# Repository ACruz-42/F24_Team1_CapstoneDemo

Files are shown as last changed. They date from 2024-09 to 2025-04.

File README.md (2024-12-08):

# SECON 2025 Hardware Competition Robot - TNTech Team

## Summary of Requirements

This repo provides the documents and reports written to produce the TNTech autonomous robot for the SECON 2025 Hardware Competition.
The following link goes to a video that shows a general overview of the requirements.

https://attend.ieee.org/southeastcon2025/wp-content/uploads/sites/642/IEEE-SoutheastCon-Hardware-Competition-Game-Mining-Mayhem.mp4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

The robot needs to autonomously navigate the field, collect materials, sort materials, deposit materials, and deposit containers.

## Capabilities

As a high level overview, the robot will need to navigate to materials outside the cave and collect them.
They will be sorted and deposited into their designated containers, which will be held by the robot.
After collecting all materials outside the cave, the robot will enter the cave.
It will then navigate to and collect materials inside the cave.
These will also be sorted and deposited into their designated containers.
After collecting all materials inside the cave, the robot will exit the cave and move to the designated zone to deposit the containers.
Finally, the robot will place a team beacon into the beacon mast.

## Salient Outcomes

Robot hasn't been constructed yet.

## Project Demonstration & Images

Picture pending of 3d model.

Give a link to a video of the project being demonstrated. The video should be hosted on the capstone youtube.

Below the video link show some well-taken, appropriately sized images of the project.

## About Us

### Team

Give a brief bio for each team member and their broad contribution to the project (no need to be terribly specifc).

Sean Borchers
Alexander Cruz
Samuel Hunter
Alejandro Moore
Dakota Moye

### Faculty Supervisor

Syed Ali Asad Rizvi

### Stakeholders

This project is important to TNTech as a whole and specifically to the ECE Department.

### Recognitions

Some portions of this robot were based off of the modular robot made Spring 2024.

Link to repo: https://github.com/lchapman42/Control-Sensing-Wireless-Charging-Robot

## Repo Organization

Give the layout of the repo and what can be found where. Make it easy on those who are interested by making the headings of the various things in this section clickable links to the relevant folder or file in the repo.

### Reports

[Link to Reports folder](https://github.com/ACruz-42/F24_Team1_CapstoneDemo/tree/a463979d4f1928be542ba7baea590573b307fce3/Reports)

This folder includes the Project Proposal, Conceptual Design, and Detail Design.

Project Proposal discusses the high-level problem, high-level solution, specifcations, constraints, and measurements of success.

Conceptual Design discusses the solution for each subsystem with each subsystem split appropriately.
It lists the team members who work on each subsystem.
There is a block diagram to show how the subsystems connect.
There is an operation flowchart to show how the robot should be interacted with by users.
There is a high level operation flowchart that shows the general actions for the robot.

Detail Design is split into a separate document for each subsystem.
Each Detail Design discusses how each subsystem will be constructed and implemented.

### Documentation

Documentation folder has only been used for electrical schematics and 3d models so far.

In the documentaion section information regarding the documentation that is required and how it should be organized is given.

### Software

No software has been written yet.

In the software directory of the repo information regarding how each team is expected to document software can be found.

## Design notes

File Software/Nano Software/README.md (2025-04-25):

## Overview

This folder contains the final Jetson Nano code presented at the SECON 2025 Hardware Competition. The Jetson Nano code was redesigned to work as a leader or controller to the Arduino follower or responder code. The Jetson Nano had all of the control and autonomous software. The Arduino had low level interface with motors for PWM signals and for reading in most sensor data.

This folder also contains one other program that was used to test the OTOS. qwiic_otos_ex1_basic_readings.py is a copy of the example provided by Sparkfun for testing the OTOS with a python controller, such as the Jetson Nano. It has been slightly modified to only record the last data point after a set timer ends. It is not used for running the robot.

The following link goes to the Arduino Follower Software readme. This provides information on how the data is sent back and forth and how the arduino controls the lower level logic: https://github.com/ACruz-42/F24_Team1_CapstoneDemo/blob/c923fd8bf496c972fe1331faf40be674d2dc7530/Software/Arduino_Follower_Software/README.md

## Dependencies

smbus2, other otos, camera, python3.11.smth

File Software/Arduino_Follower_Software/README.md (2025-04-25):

## Overview

This folder contains the final Arduino code presented at the SECON 2025 Hardware Competition. The Arduino code was redesigned to work as a follower or responder to the Jetson Nano leader or controller code. The Jetson Nano had all of the control and autonomous software. The Arduino had low level interface with motors for PWM signals and for reading in most sensor data.

## Dependencies
1. TimerOne by Stoyko Dimitrov, Jesse Tane, Jérôme Despatis, Michael Polli, Dan Clemens, Paul Stoffregen
2. ezButton by ArduinoGetStarted.com
3. Servo by Michael Margolis, Arduino

Dependencies 1 and 2 have to be installed. Dependency 3 came preinstalled in the Arduino IDE. The first two were installed through the Arduino IDE library search function.

## Use
### Input
The Arduino Follower Software takes in a set of inputs. These are supposed to come from the Jetson Nano code, but it can be manually input. The format is a packet or string of 10 ints in format "int,int,int,int,int,int,int,int,int,int" without the quotation marks. The first two need 201 options for data type. The rest need 3 options, which means 2 bits would work. In the center column of the following table is the allowed inputs. 

One example is "50,-20,1,1,0,0,1,-1,0,1". This sets left wheel speed to forward 50%, right wheel speed backward 20%, auger forward, sweeper forward, does nothing to beacon arm, does nothing to beacon gripper, opens GSC gripper, closes NSC gripper, does nothing for GSC leaner, and moves NSC leaner to pickup angle. If one of the components is already in a specific state, it will stay in that state until sent a different one. This means everything will keep moving until told to stop. For the servo control, they will keep their angle until told to change, and then will keep that angle. The table below lists the inputs in order of placement along the packet. The table shows input to be controlled, range of input control, and what happens for that range.

In the final edition of the code, the GSC arm was not used and is manually set to be 0 in the code.

|input type|input available|input action|
|:-|:-|:-|
|left wheel speed|-100 to 100|0 to 100% speed. Negative is backwards and positive is forwards.|
|right wheel speed|-100 to 100|0 to 100% speed. Negative is backwards and positive is forwards.|
|auger forward, backward, or off|1, 0, -1|1 is forward, or desired direction. 0 is stop. -1 is backward, or undesired direction.|
|sweeper direction and on or off|1, 0, -1|1 is forward, or desired direction. 0 is stop. -1 is backward, or undesired direction.|
|beacon arm preset location|1, 0, -1|1 moves beacon arm to holding angle and is initial angle, 0 is nothing, -1 moves beacon arm to placement angle|
|beacon gripper open or closed|1, 0, -1|1 closes beacon gripper and is initial state, 0 is nothing, -1 opens beacon gripper|
|Geodinum Shipping Container (GSC) Gripper open, close, or stop|1, 0, -1|1 opens GSC gripper, 0 stops, -1 closes GSC gripper|
|Nebulite Shipping Container (NSC) Gripper open, close, or stop|1, 0, -1|1 opens NSC gripper, 0 stops, -1 closes NSC gripper|
|GSC Leaner preset location|1, 0, -1|1 is pickup angle, 0 is nothing, -1 is storing angle|
|NSC Leaner preset location|1, 0, -1|1 is pickup angle, 0 is nothing, -1 is storing angle|

### Output
The Arduino Follower Software outputs a set data when it receives a command. These are supposed to be sent to the Jetson Nano, but it can print to any serial. The format is a packet or string of 7 variables in format "bit,bit,int,int,bit,bit,bit" without the quotation marks. In the center column of the following table is the available outputs.

In the final edition of the code, the current sensors were not used and are manually set to 0 in the code.

|output type|output available|output action|
|:-|:-|:-|
|current sensor for sweeper|1, 0|1 means the sweeper has stalled, 0 means it has not|
|current sensor for auger|1, 0|1 means the auger has stalled, 0 means it has not|
|GSC pressure sensor|0, 100|0 to 100% pressure. 100% pressure is max pressure sensor can handle.|
|NSC pressure sensor|0, 100|0 to 100% pressure. 100% pressure is max pressure sensor can handle.|
|GSC limit switch|1, 0|1 means limit switch, or button, is pressed, 0 means it is not pressed|
|NSC limit switch|1, 0|1 means limit switch, or button, is pressed, 0 means it is not pressed|
|light sensor|1, 0|1 means the start LED sensor sees more light than the ambient light sensor, 0 means the opposite|

## Hall Effects
In the last edition of the code, a sorter was made to process the hall effects and object sensor. The goal was to flip the servo for the sorter flap back and forth according to the hall effects and object sensor. This ended up not working due to the hall effects having some issues discussed in the Experimental Analysis. While still in the code, sorter.cpp and sorter.h currently does nothing important.

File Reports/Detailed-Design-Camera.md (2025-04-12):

# Detailed Design for Object and Line Detetion
## Function of Subsystem
The function of this subsystem is to provide the location of the astral materials, lines, and walls on the game field, as well as read the april tags and then provide this information to Master Control, so that Master Control can plot an effecient path to pick up all astral material, as well as sort the shipping containers at the end of the match, while unsuring the robot does not collide with anything from the front.

## Specifications and Constraints 
### Specifications
1. The robot shall act autonomously [S1].
2. The camera shall detect the Nebulite [S2-vii].
3. The camera shall detect the Geodinium [S2-viii].
4. The robot shall be able to detect the walls of the arena, walls of the cave, and cave entrance. Rule S03 states that if the robot causes field damage, the team will be penalized. Detecting walls stops the robot from causing damage by moving into it. The camera will be the only sensor on the front and will need to do the listed objectives [S4].
5. The camera shall read April Tags to help with Specifications 1, 2-v, 2-vii, 2-viii, and 2-ix [C1].

These Specifications stem from the the game rules and are intended to set into strict goals the methods by which the robot will score points and therefore do well in the competition. 

### Constraints
1. The camera will be able to work in both light and dark conditions
2. In order to keep costs down the robot will only have 1 RGBD camera
3. The robot will be able detect the white lines on the game field

Constraint 1 stems from the fact that the game field will have a dark cave, which will contain astral material, and as such the robot will need to enter the cave and search for astral material.
Constraint 2 stems from socio-economic concerns, the camera will comprise roughly 15% of the robots total budget, and as such it will be advantageous if only one is used to keep costs down and allow more room in the budget for other sybsystems. 
Constraint 3 stems from the robots need to use the white lines to navigate the game field as well as score points by sorting the filled shipping containers.

## Proposed Solution
In order to meet the specifications and constraints the robot will need an RGBD camera, this camera will be able to pick out the RGB values of the astral matrials and lines on the game field against the dark background of the game field, this will help meet Specifications 2 and 3 and contraint 3.
The camera will also be able to pick out the depth, or distance from the camera, of the astral material, the shipping containers, and the walls of the game field, this will help meet Specifications 1, 2, and 3.
The information from the camera and the other sensors as on the robot will be used by an object detection algorithm to the robot where the objects are on the game field, mainly the astral material, walls, and shipping containers, this will help meet Specifications 1, 2, 3, and 4.
The image data from the camera will also be used by a line detection algorithm to find the white lines on the game field to assist in navigation and sorting of the shipping containers, this will help meet constraint 3.
Finally the image data will undergo an image processing algorithm which will allow it to read the april tags, much in the same way a phone can read a qr code from a picture or screenshot, this will help meet specification 5.

## Interface with Other Systems
The camera will connect to the Jetson nano using a USB-C 3.1 Gen 1, this connection will transfer the image data, which includes including RGB values and depth values, the camera will also be powered through this connection and will take a 5V supply[2]. 
The primary responisibility of the camera will be to find the astral material on the game field and then send its location to Navigation and Master Control for the purpose of finding an effecient path to pick up all astral material.
The next responsibility of the camera will be to find the white lines on the game field and then send their locations to Navigation and Master Control for the purposes of navigation and sorting the shipping containers. 
The camera will also be responsible for reading the april tags and sending their values to Master Control for the purpose of sorting the shipping containers into the correct telemetry zones. 
The camera will also aid in locating the walls of the game field, and will be responsible for making sure that the robot does not crash into anything from the front.
Since both Navigation and Master Control and the detection and image processing algorithms will all be housed on the Jetson Nano so all communication betweeen these algorithms will be done internally.

## Buildable Schematic
Buildable schematic

## FlowChart
A quick note for the flowchart, the robot will start and then it will go about the tasks shown in the flow chart, these tasks will continue until some kind of interrupt occurs, either all astral material will be collected, or the robot will run out of time and will need to sort the shipping containers without collecting all astral material.
Operational Flowchart

## Analysis
### The Camera
The camera will be an Intel Realsense D435 RGBD camera, this camera was chosen for its wide FOV of 87° × 58°, as well as its depth range of .3 m to 3 m. Also this camera uses stereoscopic depth technology which is needed as infrared projection technology cannot be used in conjuction with the infrared camera that is part of the game field in the cave. The camera will take a 5V voltage supply that will be transfered through a USB-C 3.1 Gen 1 connection which will also be used to transfer the image data to the Jetson Nano. This connection has a maximum information transfer rate of 5 GB per second. The cameras depth values will be greater than 98% accurate at 2 meters. The camera will send both the RGB values of the picture as well as the depth values of the picture to the Jetson Nano where these values will be used by various algorithms as described below[2].

### Object Detection Algorithm
The object detection algorithm will work similarly to many generic object detection algorithms, in that it will take an image and will scan through the pixels to find specific patterns and differences is RGB values, however it will be much simpler than most object detection values as we will be mainly trying to detect one type of object with a known size and more importantly a known RGB value and a known shape, which will be against a dark background.
This will make it easy to pick out the astral material as all the algorithm will have to do is search for that specific RGB value and the seperate each little "ball" of that color, then the algorithm will go to the depth data of the image and look at the place where it found the propor color and find the depth of that area.
Since the camera will be at a fixed place on the robot we will be able define a constant axis at the front of the robot, then using the values of RGB and depth we will be able find the angle of the astral material compared to the axis at the front of the robot and then use the depth to find the distance from the axis which will give each astral material a polar coordinate value. 
This polar coordinate value can then be transformed into cartesian coordinates on the robots internal grid system.[3]
One valuable tool that will help with this process is openCV, which is a large open source computer vision and machine learning software library[5]. Using libraries from openCV will simplify the above process greatly as there are already useful libraries written that can search for specific monochromatic colors like the ones we will need for the astral material[6].

### Line Detection Algorithm 
The line detection algorithm will work much the same to the object detection algorithm in that it will take an image as input and will use a simplified version of a generic line detection algorithm to pick out the white lines against the dark background of the game field.
Since the lines on the game field are in fixed positions the robot can use the shape and composition of these lines to determine where they belong on the game field and therefore where it is in comparison to them.
Since the lines on the game field are in fixed positions the robot can use the surrounding context such as walls to determine how far away the lines are, or in other words, the depth of the lines. Similar to with object detection we can make use of openCV where preexisting libraries exist using methods such as the hough transform to find all the lines in an image[1]. 

### Image Processing for April Tags
The image processing algorithm for the april tags will activate once Master Control sends a signal that the robot is in position, it will then scan the image much in the same way the the detection algorithms did, except it will be looking for the april tags, which should be easy to locate as it will be a box of white and black.
Once the april tag has been located it will look at the specific pixels and decode them into a number, much like a QR code scanner.
it will then send the value to Master Control along with the locations of the lines from the line detection algorithm to tell the master control which telemetry zone to put the shipping containers in[4]. As april tags are becoming more commonly used in robotics there are also preexisting libraries that can aid in reading them, that will yet again come from openCV[7]. 

### Image Processing for the Walls
The image processing for the walls is a simple algorithm that will measure the distance between the robot and the walls and will alert the robot if it gets too close to a wall. Due to the way the collection system for the astral material is being designed the camera will be the only forward facing sensor and as such will be responsible for making sure the robot does not collide with anything from the front.

## Ethics 
The camera will come as a fully built and developed device and as such full credit for camera design will be given to those responsible, the camera will also have an infrared projector which will aid in depth sensing capabilities, this infrared projector is safe for use in close proximities to humans. 
The detection and image processing algorithms will also be simplified versions of generic algorithms and as such proper credit will be given for any code or methods that are taken from other sources.
Finally the subsystem will have user manual explaining the subsystems function and operation in a way that others can clearly understand the operation of the subsystem.

## BOM
| Manufacturer | Part Number | Distributor | Part Number | Quantity | URL  |Price |
|---|---|---|---|---|---|-|
| Intel| 82635AWGDVKPMP| Intel| 82635AWGDVKPMP| 1|[Intel Realsense D435](https://store.intelrealsense.com/buy-intel-realsense-depth-camera-d435.html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)|314.00 USD|

## Refrences 
[1]“OpenCV: Hough Line Transform,” docs.opencv.org. https://docs.opencv.org/3.4/d9/db0/tutorial_hough_lines.html  

[2]“Intel ® RealSense TM Product Family D400 Series Datasheet Intel ® RealSenseTM Vision Processor D4, Intel ® RealSenseTM,” 2024. Available: https://www.intelrealsense.com/wp-content/uploads/2024/10/Intel-RealSense-D400-Series-Datasheet-October-2024.pdf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  

[3]“What is Object Detection in Computer Vision?,” GeeksforGeeks, May 10, 2024. https://www.geeksforgeeks.org/what-is-object-detection-in-computer-vision/  
‌  
[4]X. Ling, “How to Optimize QR Recognition Performance by Image Preprocessing and Parameter Tuning,” DEV Community, Sep. 13, 2021. https://dev.to/yushulx/how-to-optimize-qr-recognition-performance-by-image-preprocessing-and-parameter-tuning-24p8 (accessed Nov. 28, 2024).

[5]OpenCV, “About OpenCV,” OpenCV, 2018. https://opencv.org/about/

[6]“Real time object color detection using OpenCV,” GeeksforGeeks, Oct. 14, 2021. https://www.geeksforgeeks.org/real-time-object-color-detection-using-opencv/

[7]A. Rosebrock, “AprilTag with Python,” PyImageSearch, Nov. 02, 2020. https://pyimagesearch.com/2020/11/02/apriltag-with-python/
‌
‌
‌
‌
‌
‌

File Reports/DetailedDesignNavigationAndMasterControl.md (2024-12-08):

# Detailed Design
## Function of the Subsystem

The navigation and master control subsystem utilizes a Jetson Nano as the core of the robot's systems. The master control portion of this subsystem interfaces with the various sensors, such as the LiDAR and OTOS (Optical Tracking Odometry Sensor) sensors, and motor control. The navigation portion of this subsystem is based on an internal 2-dimensional grid. Based on the positional feedback from the sensors and event completion feedback from the Arduino microcontroller parsed by the master control subsystem, the navigation subsystem outputs a desired rotation and distance that the master control subsystem sends to the motor control Arduino in the form of high-level serial commands over a USB connection. Additionally, with the assistance of the Sensors and Object Detection subsystems, respectively, this subsystem will handle localization of the robot (i.e. its position on an internal map of the game board) and the placement of the astral material on the robot's internal map. It will manage all of this using a state machine that transitions its states based on the time remaining and positional feedback from the various sensors and event completion feedback from the  motor control Arduino.

## Specifications and Constraints

### Specifications:
1.  The Robot shall act autonomously (Specification 1 [1]). This is necessary for compliance with Game Manual 1
2.  The Robot shall be able to navigate to and position itself for the following tasks (Specification 2 [1]). This is necessary to maximize potential points.
	i. Navigate out of Landing Pad (i)
	ii.  Navigate within 3 seconds of Start LED (ii)
	iii.  Navigating into the cave (iii)
	iv.  Navigate to correct shipping pad (v)
	v.  Navigate to and allow for placement of team beacon (ix)
3.  The Robot shall account for background interference (Specification 11 [1]). This is to help reduce potential failure points.
### Constraints:
1.  The Robot shall stay on the game field (Specification 5 [1]). This is necessary for the safety of the team and all IEEE SECON staff members.
2.  The Robot shall cease all operation after 3 minute timer is done (Specification 10 [1]). This is necessary for the safety of the team and all IEEE SECON staff members.
3. The Robot shall immediately cease operations upon the usage of the emergency stop button (Specification 7 [1]). This is necessary for the safety of the team and all IEEE SECON staff members.

## Overview of Proposed Solution

The proposed solution centers around a hybrid navigation system combining preprogrammed paths with dynamic pathfinding for specific tasks. The system relies on a state machine and an event queue to generate and coordinate high-level navigation commands with the microcontroller associated with the motor subsystem. Sensor feedback from LiDAR and odometry ensures real-time localization and adaptive positioning.

### **Core Components and Operation**

1.  **State Machine**  
    The majority of the robot's navigation tasks, such as moving between predefined locations like the landing pad, cave, and shipping pad, are handled via preprogrammed paths defined in a state machine. A state machine is a way of organizing potential states that, in this case, the robot can be in, and the transitions between these states. The routes these states mean algorithmic pathfinding can be avoided, reducing the need for heavy computation during a match.
    
   2.  **Event Queue**  
The event queue serves as a decoupling mechanism, separating the state machine and high-level logic from time-sensitive tasks [2]. Once a desired position or action is determined by the state machine, it is added to the event queue. The queue then processes these events sequentially, sending high-level commands—such as the required rotation and distance—to the microcontroller, which handles motor control. After the Arduino sends a command saying it's processed the current event or a period of time without movement, the next event is sent. This design allows the Jetson Nano to continue processing other high-level tasks, such as processing sensor data or computing navigation algorithms. 

2.  **A-Star Pathfinding**  
    The A-Star algorithm is employed for states that involve picking up astral material. The way that A-Star works is as a form of Dijkstra's algorithm (an algorithm that explores each node in order of its distance from the starting node) [3]. In essence, A-Star is used as a way to balance finding the shortest path along with a given heuristic (in this case, proximity of the path to the nearest material) [4].  The state machine chooses the furthest astral material. A-Star plots a path to this material. The heuristic function in the A-Star algorithm heavily prioritizes paths  with astral material. If any astral material remain after reaching the destination, this process is repeated until either all astral materials are gathered or the time allotted runs out. This approach balances optimal pathfinding with the competition's time constraints, allowing the robot to maximize points.

4. **Sensor-Driven Feedback Loop**  
    Positional data from LiDAR and odometry sensors provide continuous updates on the robot's location. This feedback ensures that the robot can accurately determine its current position and orientation, enabling adjustments when moving toward desired positions.

### **Specification Compliance**

1.  **Autonomous Operation (Specification 1)**  
    The competition forms the basis for various setpoints (static positions of the shipping containers, entering the cave, or the dynamic positions of the astral materials) . Based on these internal setpoints and feedback from the sensor subsystem and motor control subsystem, the robot utilizes a state machine to generate setpoints for the motor control subsystem. The event queue decouples the generation of these setpoints from time, and instead couples the generation with the completion of prior setpoints. The integration of the state machine, event queue, and sensor feedback ensures that the robot operates autonomously, meeting the competition’s requirements for compliance with Game Manual 1.
    
2.  **Navigation (Specification 2)**
    - Preprogrammed paths handle transitions between key locations (e.g., specifications i, ii, iii, v). The state machine holds desired positions, which the event queue determines the necessary distance from the actual position of the robot, and necessary rotation to get to that position.
    - The A-Star algorithm dynamically optimizes the collection of astral materials by balancing path length and material prioritization (e.g. specification iv, and for the collection of astral material). A heuristic that balances path proximity to astral material versus the cost of the path will be determined experimentally to find the lowest time. This can and will be done both with the physical robot, and via the Godot simulation.

3.  **Background Interference Tolerance (Specification 11)**  
    The feedback loop continuously corrects the robot's position using real-time sensor data from multiple sensors and an event completion signal from the motor control Arduino, mitigating the effects of environmental interference such as noise.

### **Constraints Compliance**    

4.  **Staying on the Game Field (Constraint 1)**  
    Predefined paths plot a course that should keep the robot within the boundaries. Real-time sensor data from the LiDAR ensures the robot stays within boundaries as a stop command will be issued to the Arduino within a certain distance, maintaining safety for participants and compliance with rules. 
    
5.  **Ceasing Operation (Constraint 2)**  
    The state machine halts all operations when the timer reaches the three-minute limit. This is currently enforced programmatically as a high-level if statement inside of the main loop of the program.
    
6.  **Emergency Stop (Constraint 3)**  
    The emergency stop button overrides all active processes, immediately issuing a stop-motors command to the Arduino, ensuring compliance with safety requirements.
## Interface with Other Subsystems

#### Inputs:
-   **LiDAR Data**: Provides distance measurements to surrounding objects for real-time localization and obstacle detection.
    -   _Input Type_: Distance
    -   _Method_: I2C

-   **Odometry (OTOS) Data**: Applies Kalman filter to IMU, and optical sensor, and outputs the result.
    -   _Input Type_: Positional
    -   _Method_: I2C
   - **Arduino Data**: Provides signal that a given event has completed, or stopped prematurely.
       -   _Input Type_: Signal
	    -   _Method_: USB
   - **Camera Data**: Uses color to determine where astral materials are on screen, then uses depth to output position of astral material. 
       -   _Input Type_: Positional
	    -   _Method_: USB
  #### Outputs:
  
 -  **Rotational Setpoints**: Tells Arduino how far to rotate robot.
	 - _Output Device_: Motor Control Arduino
	 - _Output Type_: High-Level Commands
	 -  _Method_: Serial
-  **Positional Setpoints**: Tells Arduino the distance of translation for robot.
	 - _Output Device_: Motor Control Arduino
	 - _Output Type_: High-Level Commands
	 -  _Method_: Serial
- **Stop Command**: Tells Arduino to stop immediately, in case of collision or match end.
	 - _Output Device_: Motor Control Arduino
	 - _Output Type_: High-Level Command
	 -  _Method_: Serial
## Godot Simulation
As a proof of concept for the overarching software architecture, a simulation in Godot was created. Godot was chosen for two main reasons: ease of prototyping, and the similarity of GDScript (Godot engine's inbuilt programming language) to Python. Additionally, closure (the ability for a function to retain memory outside of its enclosing scope [5]) makes the connection between state machine and event queue easier. At time of writing, this simulation is not fully operable but development is ongoing and the most up to date version (and source code) can be found at the following link. Note that support for operating systems other than Windows is not supported at this moment.

https://github.com/ACruz-42/F24-Team1-Capstone-Simulation

The state machine is only about half-way complete, but the relationship between main loop, state machine, and event queue are functional and proofs of the effectiveness of the design. That is to say, the state machine correctly outputs desired positions and rotations, but does not currently contain all states as described in the operational flow chart below. Additionally, the A-Star algorithm works but is not interconnected with the other subsystems at this moment. 
## Buildable Schematic

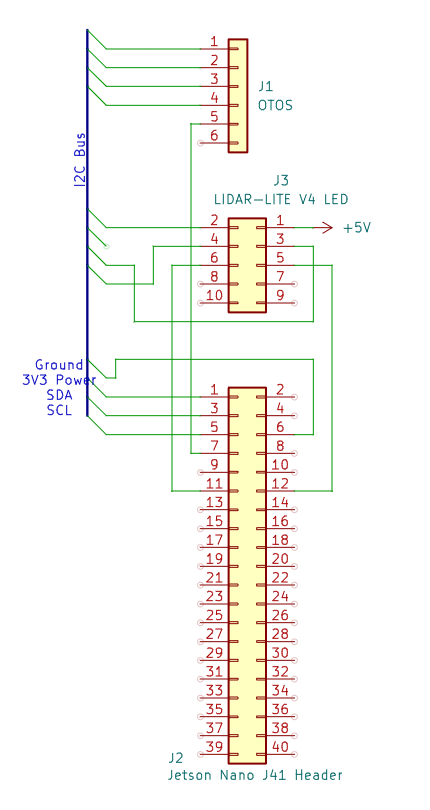
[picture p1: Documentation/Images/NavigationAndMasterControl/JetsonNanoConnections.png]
GPIO Pinout for Jetson Nano

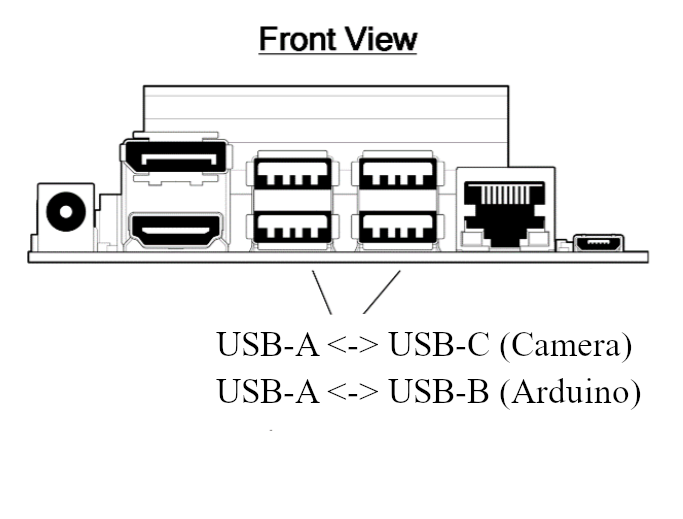
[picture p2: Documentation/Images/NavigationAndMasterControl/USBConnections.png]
Jetson Nano USB Connections

## Operational Flowchart

Operational Flow

## Hierarchy

### Highest
- **State Machine**: This provides the setpoints for the rest of the system.
	- **Event Queue**: This parses the sensor and camera subsystems, interprets the state machine's setpoints with respect to the current state, then sends commands (target location setpoints) to the Arduino.
		- **Sensor Subsystem**: This provides positional feedback to event queue.
		- **Camera Subsystem**: This provides positional feedback to event queue (with respect to astral material).
			- **Arduino**: This receives setpoints, initiates a PID control loop with the motors, then provides feedback to the state machine that the motors have finished.
				- **Motors**: The motors deliver rotational energy to the wheels, which move the robot. The related encoders provide velocity feedback to the Arduino.
### Lowest

## BOM

|Item|Manufacturer|Part Number| Distributor|Distributor Part Number|Quantity|Price
| :- | :- | :- | :- | :- | :- | :- |
|Jetson Nano|Nvidia|#945-13450-0000-100|Amazon|B0B8DMPWJL|1|$215
|Total||||||$215|

Jetson Nano purchasing link: https://www.amazon.com/onboard-Robotics-Machine-Learning-Version/dp/B0B8DMPWJL

## Analysis

-   **Program Structure: State Machine, Event Queue, and Main Loop**  
    The decision to structure the software into a state machine, event queue, and main loop provides several advantages in maintainability and efficiency.
    
    -   The  state machine dictates the robot's high-level behavior, handling navigation between predefined locations and managing of transitions predictably and reliably. Additionally, clear delineations between states allow for easy debugging and experimentation
    -   The event queue serves as a time-independent intermediary, decoupling the state machine from real-time motor control. By abstracting motor commands to the Arduino, the event queue allows the Jetson Nano to continue executing high-level tasks without being constrained by execution delays.
    -   The main loop integrates the state machine and event queue together, ensuring continuous processing of sensor data and high-level commands. This structure ensures the robot can react dynamically to new information without compromising ongoing tasks, such as the operation of the emergency off-button or the detection of astral material. This design has already shown promise in the Godot simulation, where the interdependencies between these components have been successfully implemented, even if partially.
-   **Choice of Godot for Simulation**  
    Godot was selected as the simulation platform for its ease of prototyping and its GDScript language, which closely resembles Python—the programming language used on the Jetson Nano. This similarity allows for a smoother transition from simulated logic to real-world implementation.
    
    -   **Prototyping**: Godot’s user-friendly interface and node-based structure made it possible to iterate on designs quickly, enabling fast debugging and validation of core concepts such as the interaction between the state machine and event queue.
    -   **Code Translation**: GDScript’s support for closure simplifies the connection between the state machine and event queue. Python is similar in both its indent-based code, and programming with support for closure. This structural alignment ensures the simulation’s code can be easily transferred to the actual robot.
    -   **Progress**: While the simulation is not fully operational, its current development demonstrates the effectiveness of the chosen structure. The integration of A-Star for astral material collection and the foundational elements of the state machine are already functional, further validating this choice.
    
    The simulation also provides a controlled environment to test edge cases and refine the robot’s behavior before physical implementation, significantly reducing development risks.
    
-   **Jetson Nano Over Raspberry Pi 5**  
    The Jetson Nano was selected over the Raspberry Pi 5 due to its superior compatibility with AI and machine vision tasks and its lower power consumption.
    
    -   **Processing Capabilities**: The Jetson Nano’s GPU is optimized for deep learning and computer vision tasks, enabling efficient real-time processing of sensor data (particularly the camera) and the A-Star algorithm. This capability directly supports the subsystem’s need for parallel computational power, particularly for tasks like localization and navigation.
   
    -   **Power Efficiency**: Operating between 10-20W, the Jetson Nano consumes significantly less power than the Raspberry Pi 5’s 25W, aligning with the project’s constraints on battery life. This efficiency ensures the robot can operate effectively within the competition’s time limit without exhausting power resources.

## Execution Plan

The current execution plans revolves around finishing the Godot simulation. The navigation portion of the navigation and master control subsystem should be trivial with the ability to use the GDScript code as a reference. Once all the ordered parts arrive, more importance will be placed on integrating the Jetson Nano with the various sensors and connection to the Arduino. By swiftly implementing the master control subsystem, development on the other subsystems can take place faster.

The simulation should, assuming current development pace, be finished before next semester.

The parts necessary for the other subsystems should arrive by the next semester.

Although the competition takes place in March, the plan is to finish by February and test during its duration. This leaves January and February to implement the navigation and master control systems. As the navigation subsystem should be easily transferrable, and the master control subsystem will be implemented with the assistance of the other subsystems, completing the robot should be a viable task.
## References

[1] “Game Manual 2 V1.1.3,” IEEE, 2019. Accessed Nov. 26th, 2024. [Available Online] https://docs.google.com/document/d/1fN7bsJFpCJur66JkueRHXtlybt0m7QSY4Nn62lHAnrc/edit?tab=t.0
‌[2]R. Nystrom, “Game Programming Patterns”. United States. Genever Benning, 2014.
[3] GeeksforGeeks, “Dijsktra’s algorithm,” GeeksforGeeks, Nov. 19, 2018. Accessed Nov. 26th, 2024.  [Available Online] https://www.geeksforgeeks.org/dijkstras-shortest-path-algorithm-greedy-algo-7/
[4] “A* Search Algorithm in Python,” GeeksforGeeks, Apr. 17, 2024.  Accessed Nov. 26th, 2024.  [Available Online] https://www.geeksforgeeks.org/a-search-algorithm-in-python/
‌[5]Rahul K, “An Introduction To Closures and Decorators in Python,” Earthly Blog, Jul. 18, 2023. Accessed Nov. 26, 2024. [Available Online]https://earthly.dev/blog/python-closures-decorators/

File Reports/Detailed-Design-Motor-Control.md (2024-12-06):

# Detailed Design
## Function of the Subsystem 
The motor control subsystem is meant to carry out the functions of the robot based on sensory input and the needs of the given situation during the competition as driven by the Master Control. The drivetrain motors will actuate the translation of the robot and will change the speed based on factors such as weight, obstacles, time remaining, among other crucial considerations for obtaining the maximum amount of points. Additional mechanisms on the robot will be used to collect, sort, and distribute astral material in their appropriate containers. These mechanisms will also require motor control, and they will use various types and configurations of motors. 

The drivetrain motor system functions as the feedback-based reaction center for the robot’s processes. It uses the input taken in from sensory data, such as object and line detection or map navigation, and follows the commands given to it from a microcontroller to perform the physical responses of the robot. Motor control can include the following components: a microcontroller (MC), motor, motor driver, encoder, power supply, and specific components for noise reduction and circuit protection [1]. The motor microcontroller carries the digital signal commands for the designated motor to operate as required. However, the power that the MC needs to function is not enough in comparison to what the motor needs. Therefore, it is essential to have a component that can step up the power for the motor while still using the MC for commands. This is the purpose of the motor driver. The motor microcontroller sends a digital signal to the driver using PWM to set the desired motor speed. Encoders that detect the motor shaft speed/position to provide the actual speed of the motors are useful for completing a closed loop feedback system, such as with PID control [2]. All logic control circuitry, which includes the microcontroller and encoders, will receive low voltage from the power subsystem, while the motor driver will receive high voltage in order to provide the high power needs of the motors. 

Several types of motors are utilized for the astral material collection and sorting process. Brushed DC motors are used for the mechanisms that have continuous feedback based on desired versus actual motor speed, such as with the overall robot movement and the collection of astral material. Separate motor drivers are connected to these motors and provide the appropriate power based on PWM input from the microcontroller. Linear actuators will be used for clamping onto the shipping container, and they will need drivers as well for directional control of the extension of the actuator. Servo motors will be used for the material sorting mechanism via a system of gates, lifting the shipping container, and controlling the positioning of an arm that will place the Team Beacon.  

The selection process for choosing a brushed DC motor versus a servo motor for the collection and sorting applications is based on the torque and speed requirements of each system. For the drivetrain motors, the motor control system will be constantly running and collecting feedback, going at a high speed and changing directions quickly. Therefore, a circuit that can efficiently modify the power level to the motors would be ideal, and a brushed DC motor/driver pairing using PWM control would satisfy the need for efficient speed control. However, there will be a need for motors that are not continuously running and collecting data but may instead be performing a precise sequence of movements that are based on position control and feedback. This is where a servo motor would prove to be useful, as the servo position is able to be finely controlled by applying the correct pulse length from the microcontroller [4]. Both brushed DC motors and servo motors have high torque applications, but with different usage cases. Brushed DC motors will have high torque at a low speed [12], likely due to a heavy load. Servo motors will also have high torque for heavy loads, but the context for their use will be in precise positional control over the mechanism that carries the load. Servos also have three different sizes depending on desired torque level: micro, standard, and giant [4]. Micro and standard sizes will be used for the mechanisms discussed in this report. 

## Specifications and Constraints 
#### 1) The motors shall be capable of meeting the requirements of the Game Manuals and shall be appropriate for their designated mechanisms (detailed below). 

#### 1a) The motors shall operate at a voltage of less than 30 volts [S12]. 

Rationale: This voltage limit was put in place due to the requirements placed by Game Manual 1 at Rule 16 for the purpose of safe but capable robot operation. 

#### 1b) The drivetrain motors shall be able to accelerate up to a calculated desired speed for each navigational path that can enable the robot to traverse the whole field twice in under 3 minutes using a given distance, angle of approach, and the time allotted. 

Rationale: This specification was put in place to verify the capabilities of the motors for efficient speed control and to create a plan for the Motor Control subsystem to meet the objectives set by Navigation and Master Control.  

#### 1c) The motor specs for each mechanism shall account for a proper balance of speed, torque, and inertia to implement the best-suited motors for the task. 

Rationale: This balance was considered because even though some components and methods may meet general specifications, the goal is to search for the best solution that can optimize the overall process for collecting points.  

#### 1d) The drivetrain motors shall be able to operate under a load of up to 12 kg. 

Rationale: The 12 kg threshold is the maximum allowed mass permitted for the heaviest configuration of the robot, as per Game Manual 1. 

#### 1e) The sorting and collecting motor systems for astral material shall be able to transfer and carry the load of at least one astral material at a time (3D printed icosahedrons, 48.2 g each for Geodinium). 

Rationale: In order for the sorting and collecting process to function, at least one astral material must be able to traverse the whole system from pick-up to deposit at a time, and therefore the mass of at least one astral piece will be considered for load-handing from the motors. 

#### 1f) The Cosmic Shipping Container motors shall be able to carry and support most of the load from a full container of astral material – 18 Geodinium for a total of 867.7 g. 

Rationale: A full container of material accounts for the worst-case load scenario for the motors, with Geodinium being slightly heavier than Nebulite due to the internal magnets. 

#### 2) The motor control subsystem shall be capable of an immediate termination of functions induced by an emergency stop button [S7]. 

Rationale: This command for immediate stoppage brought about by E-Stops is required by the Game Manual 1 at Rule R04 and enables increased protection for the equipment, arena, and personnel on site.  

#### 3) The motors shall be capable of speeds allowing the robot to traverse the game field at least twice (once for collecting astral material, and once for the return trip) within three minutes (the length of a match) [S2]. 

Rationale: This specification was put in place so that the robot would be equipped to at least reach any point on the map and return to deposit material for points. On this one trip, the current plan is to find the most optimal route around the field for material collection, but making it so that the robot would have the ability to quickly and efficiently traverse the entire field and back would account for any suboptimal deviations within the time limit. 

#### 4) The motors shall be capable of reversing the robot in the case that reversing the robot is the only method of not damaging the game field walls [S4]. 

Rationale: This was of consideration due to the need for the robot to be able to have escape maneuverability near field walls, with damage to the field being grounds for a penalty.  

#### 5) The motor subsystem shall be designed in such a way that accounts for background interference in the competition environment [S11]. 

Rationale: This specification was put in place due to the requirement set by Game Manual 1 at Rule R13, in which competitors should account for naturally occurring electrical noise in the competition environment that may interfere with the lower-level circuitry.  

#### 6) The motor subsystem shall have a user manual that explains functionality and design intent [C2]. 

Rationale: This specification was placed in order to follow a precedent set by prior capstone groups for creating documentation that lays out the necessary design information for any future work on a similar project or building on the same project.  

#### 7) The motor subsystem shall adhere to applicable requirements in standard IEC 60204-1 pertaining to electrical supply, electromagnetic compatibility, emergency stop, and control circuit protection [C3]. 

Rationale: This constraint was put in place for the motor subsystem to abide by established electrical codes, with this particular IEC standard laying out several different types of safety measures that would be applicable to the motor control circuitry. It aligns with the request from the Game Manuals in the mandatory inclusion of E-Stops. It also presents the necessity to include components that promote overcurrent protection and proper grounding [3]. Clear labels and documentation for the circuit components involved are also needed by this standard [3].  
 
## Overview of Proposed Solution
### Drivetrain
The solution will incorporate several layers of command for the robot movement. The first layer will involve the Arduino Mega microcontroller, which will process the logic for the PID control of the drivetrain motors. The PID parameters will be adjusted by the Mega after it calculates the error between the desired and actual speed. The motor driver that will be used to carry out the speed adjustment from the Mega is the Pololu Dual VNH5019 Motor Driver. This driver acts as a regulator for how power is used between the 12V source and the motor, using a PWM command that resulted from the speed adjustment. This motor driver is compatible with Arduino, and it can control two bidirectional brushed DC motors. The bidirectional property fulfills Specification 4, regarding the request to be able to have forward and backward control for each motor so that the robot can escape potential obstructions and damage the field. As far as braking is concerned, electrical and mechanical braking are the main types to select from. Electrical braking would be better suited for DC motor control because of efficiency, less heat production, and higher permitted speeds/loads [17]. The types of electrical braking include regenerative braking, dynamic braking, and plugging. Regenerative braking involves exceeding the no-load speed of the motor to the point where the motor current reverses and the motor becomes a generator for the battery. Dynamic braking disconnects the power supply, and a braking resistor connects across the armature and takes the heat generated by the electrical energy that came from the remaining kinetic energy of the motor. Plugging takes place when an excited DC motor reverses the armature terminals or the polarity of the supply, which orients the supply and induced voltages in the same direction and doubles the supply voltage [17]. Regenerative braking is the most efficient of the three, as it would use some of the remaining generated energy from the motor to replenish the battery life of the robot. Therefore, regenerative braking is the option that will be pursued.  

The motors that will be used are two 12V Metal DC Geared-Down Motors with built-in incremental encoders. These motors operate at a max of 12V, which fulfills Specification 1 of not exceeding the competition 30V limit. The VNH5019 driver is compatible with voltage ranges from 5.5 to 24 V, fitting the 12V motor spec. The stall current of the motor is 5.5A, and the current rating per motor for the VNH5019 is 12A, meaning that the maximum possible motor current is well within a safe threshold with this driver. The driver also has built-in overcurrent protection, reverse-voltage protection, and current sensing, which addresses the IEC 60204-1 standard constraint for safe electrical practice in the control of the motor subsystem. Electrical components such as a switch and fuse can be installed on the power line to the motor driver so that the E-Stop request from Specification 2 and IEC 60204-1 can be fulfilled and overcurrent risk can be mitigated. A user manual based on the design report documentation can be created, fulfilling Specification 6. Specification 5 can be fulfilled through proper grounding and electrical shielding/isolation techniques. As far as range is concerned, in addressing Specification 3, the chosen motor will have specs provided that can be used to calculate the motor speed, wheel speed, and resulting time taken for the robot to traverse the entire field twice. The results of said calculations are present in the Analysis section. 

The remaining requests for Specification 1 can be satisfied through breaking down motor specs and calculating the required speed for the robot to successfully traverse the field, collecting as many points as possible in the 3-minute timeframe. The 12V DC motors for the drivetrain have a stall torque of 21 kg/cm, which implies that with two of these motors providing this torque for a total of 42 kg/cm, this motor will be able to satisfy the 12 kg load requirement at 1d. The motors also provide enough speed to accomplish the 3-minute path goal, as described in the Analysis section, helping address Specification 1b and part of 1c. The inertia is the main item that is not calculated for 1c, but it is stated in a product review (link in the budget) to have high inertia. The review also states that a steady reduction of power or early stoppage can help mitigate this potential issue.  

### Collecting and Sorting Process
The mechanisms dedicated to collecting and sorting the astral material are primarily being designed by the Mechanical Engineering team, but the motor control for each mechanism will still be addressed here.  

At the start of the collection process, the Cosmic Shipping Containers will be picked up by two clamping arms for secure transport as the robot searches for astral material. The clamping mechanism will involve two linear actuators that will be regulated in speed and direction by their own respective motor drivers, which are controlled via PWM signals from the Jetson Nano. The actuators will receive a signal from a limit switch, placed at the ending extension point for one of the actuators, so that they can detect when the actuator reaches the desired compression length for the container. Two pressure sensors will be placed at the extremities of the actuators to quantify the compression applied. In order to lift the Cosmic Shipping Containers, two servo motors will be used on an arm that will lift the container and lean it against the base of the robot for transport. These servo motors will have their angle of inclination controlled directly by a PWM connection to the Arduino Mega. The servos can handle 29 kg/cm at 5.0V, which is well above the requirement from Specification 1f.  

In order to collect astral material and put it into the correct container, there will be a roller, similar in form to a vacuum roller, at the front of the robot that will sweep up material and place it into an auger. The auger will pull up astral material, one by one, and deliver them to a sorting area. In this stage, the solution includes two brushed DC motors with each having their own motor driver, one for the speed and direction of the roller and another for the speed and direction of the auger. The drivers will be controlled via a PWM signal from the Arduino Mega.  

In the sorting stage, each astral material will go through a chute that has two gates. The first will catch the astral piece from going any further and have it scanned by three surrounding Hall Effect sensors that will determine whether it is the magnetic Geodinium or the non-magnetic Nebulite. There are two chutes for each type beyond this gate, with another gate in between that flips to one side or the other based on the type scanned. In this solution, there are two servo motors that will be implemented, with each servo driving each of the two gates. The position of the servos will be determined by a PWM signal from the Arduino Mega. These servos can handle 2.0 +/- 0.20 kg*cm at 4.8V for stall torque, showing that the threshold for the Specification 1e load would safely be met. 

Finally, the Beacon Arm will be a 1 degree-of-freedom arm that will swing out from the robot, holding the Beacon during the swing, and place the Beacon at the Beacon Mast in the middle of the west wall of the field. The motor solution that would be implemented for this includes two servo motors, one for the arm and one for the grabber, that would be controlled by PWM directly via the Arduino Mega. The team has yet to fully commit to the Beacon Arm, but this would be the solution in the event that it would be feasible to include.  

## Interface with Other Subsystems
### Drivetrain
The motor control subsystem will communicate primarily with the Jetson Nano microcontroller, designated as the Master Control. The Arduino Mega that houses the motor control processes will transfer serial data commands and information via a USB connection between the Nano (USB-A) and Mega (USB-B). Inputs from the Nano to the Mega will include desired motor speeds and directions, along with override commands to halt motor control processes in case of encountering obstructions (such as a wall) or running out of time. Outputs from the motor control subsystem to others will primarily be in the form of data updates to the Nano about motor performance and actual speed. The Mega will use the properties of the encoders to track the positioning of the motor shaft and report rotational position data that can be converted into the actual speed, given the logged time frame. The Mega will be using this reporting to make onboard adjustments to the motor speed using PID control, attempting to match the set desired speed. The Nano will keep track of the reported actual speed to understand the current state of the robot and how it should continue to implement sensor data.  

Aside from Master Control, the Motor Control subsystem will also receive inputs from the Power Management subsystem. The motors are 12V and will vary in power usage based on the VNH5019 Motor Driver module. 12V will be sent from the power circuit to the driver. The logic circuitry of the driver and the Arduino Mega will require a step down to 5V. Therefore, a buck converter that steps down the maximum supplied voltage of 12V to 5V will be connected between the power circuit and driver/ Mega as well.

### Collecting and Sorting Process
For each of the mechanisms that involve servo motors, the input going into the motor will come from PWM connections at the Arduino Mega. These mechanisms include the sorting gates, lifting arm, and Beacon arm. The type of data transmitted is positional data for the angle of inclination of the servo, controlled by the width of the PWM signal [4]. Regarding feedback, the servos that will be used have built-in potentiometers that give feedback on actual positional servo data [4].Power inputs for the servos are rated at 5V. For the mechanisms that involve brushed DC motors and drivers, which are the linear actuator and roller-auger stage, a PWM signal will be sent from the Arduino Mega as an input to the drivers for speed and direction control. Power inputs for the motor drivers are rated at 12V. The pressure sensor will transmit analog data to the Arduino Mega, while the limit switch will transmit a digital signal indicating whether a trigger was activated.  

## 3D Model of Custom Mechanical Components 

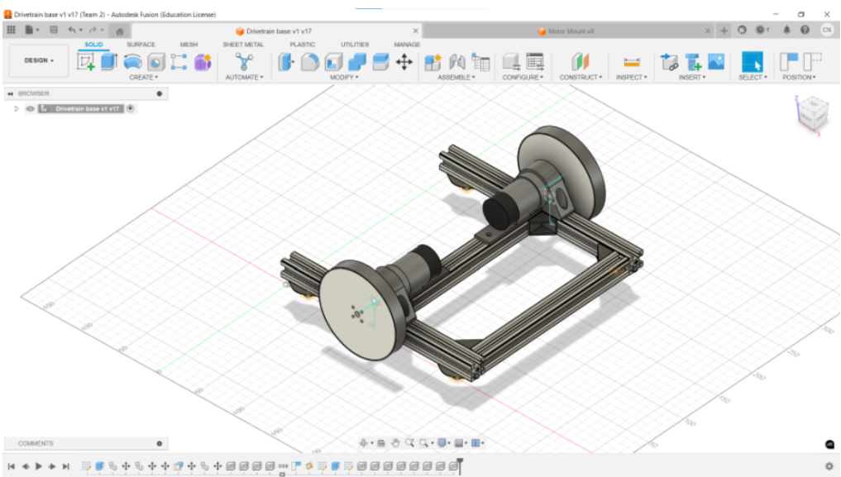
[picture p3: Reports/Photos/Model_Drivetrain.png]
Model_Drivetrain

This is a 3D model of the drivetrain for the robot, placed at the center of the overall robot frame. There are two drive wheels attached to brushed DC motors that enable the robot to move forward, backward, and rotate at a point. This model was constructed by Cooper Nelson on the Mechanical Engineering Team. 

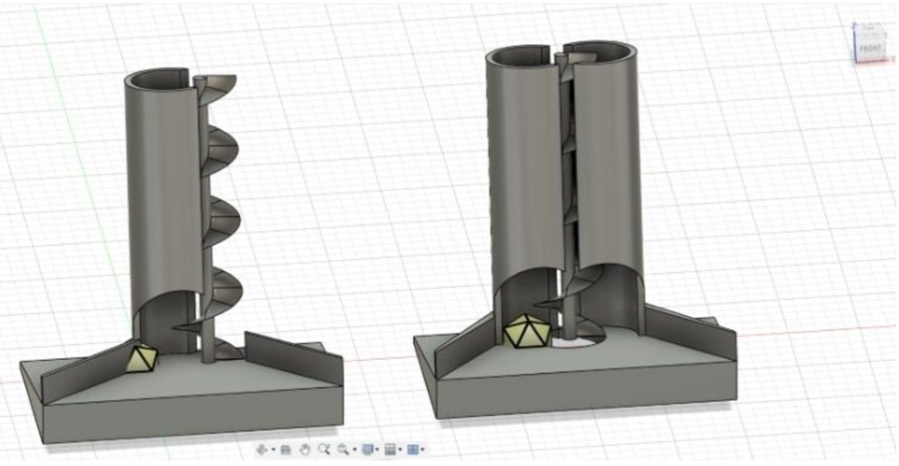
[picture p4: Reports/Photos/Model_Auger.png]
Model_Auger

This is a 3D model of the Auger and Hopper (staging area) for the astral material to be picked up from the Roller collection, one by one, and taken up to the top. After reaching the top, the material will be deposited into the sorting area. This was designed by Caleb Sullivan on the Mechanical Engineering Team. 

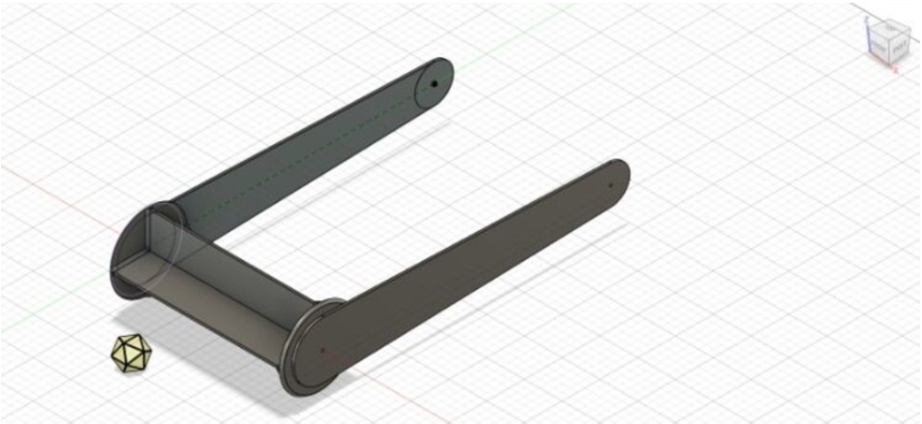
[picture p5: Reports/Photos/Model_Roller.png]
Model_Roller

This is a 3D model of the Roller/Sweeper mechanism, with an astral material piece at the front for reference. The material will get swept into the Roller, in a similar fashion as with a vacuum cleaner. This model was constructed by Caleb Sullivan on the Mechanical Engineering Team.  

## Buildable Schematic
The following diagram connections were informed by [6], [8], [9], [10], and [11].  

### Drivetrain Subsystem
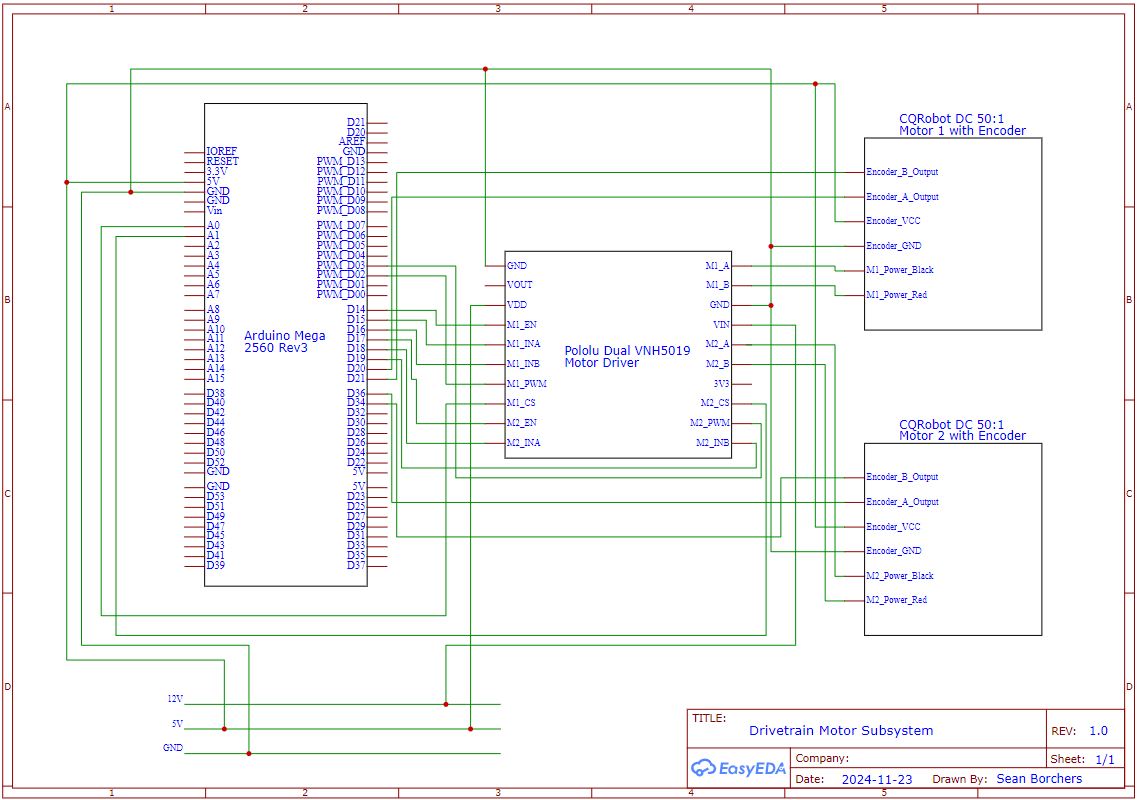
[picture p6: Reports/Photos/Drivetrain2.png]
Drivetrain2

### Servo Motor Mechanisms
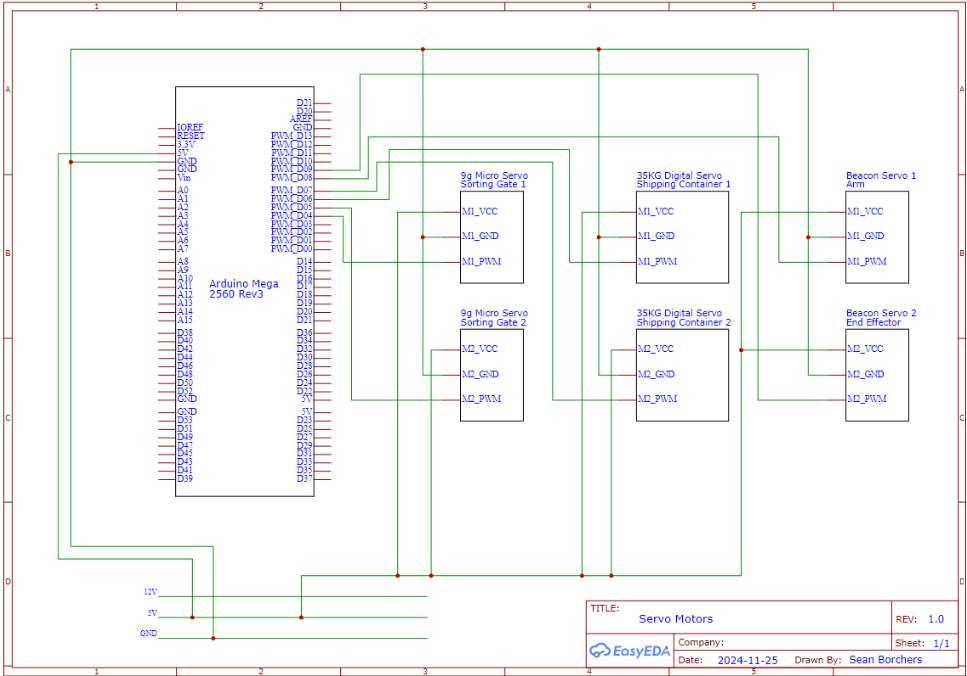
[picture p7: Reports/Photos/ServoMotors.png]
ServoMotors

### Auger and Roller Mechanisms
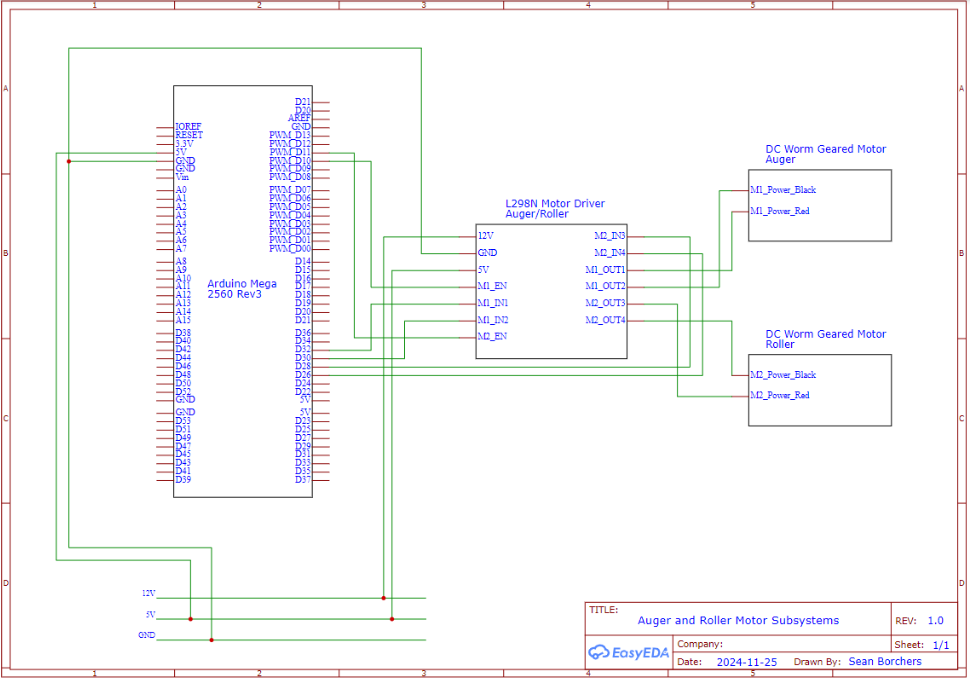
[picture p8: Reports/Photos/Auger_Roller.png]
Auger_Roller

### Container Lift Mechanism Using Linear Actuators
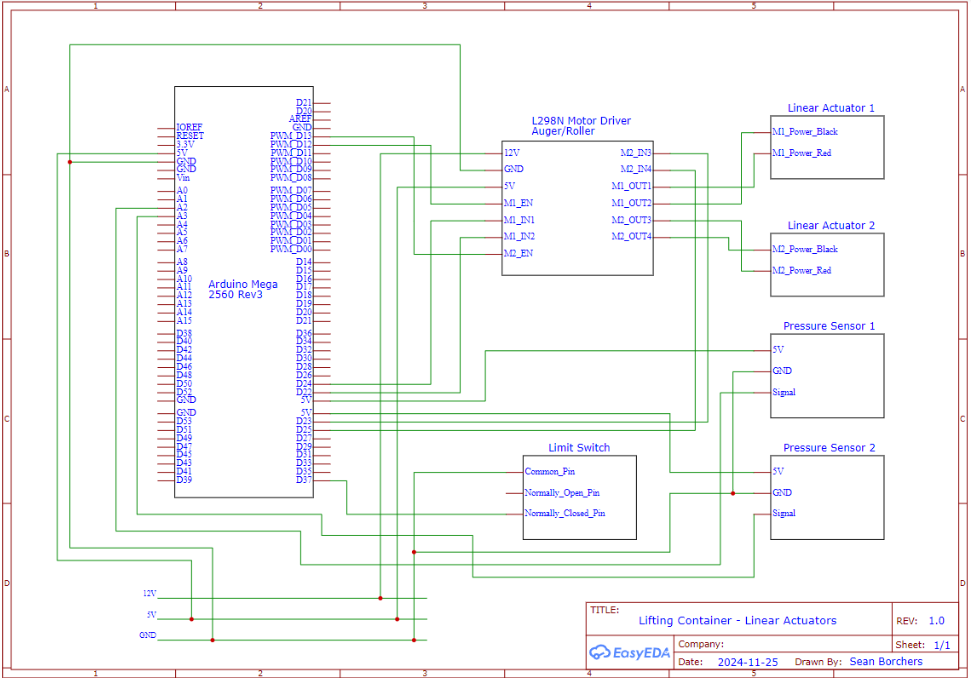
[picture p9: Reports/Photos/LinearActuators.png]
LinearActuators

## Operational Flowchart
### Drivetrain PID Loop
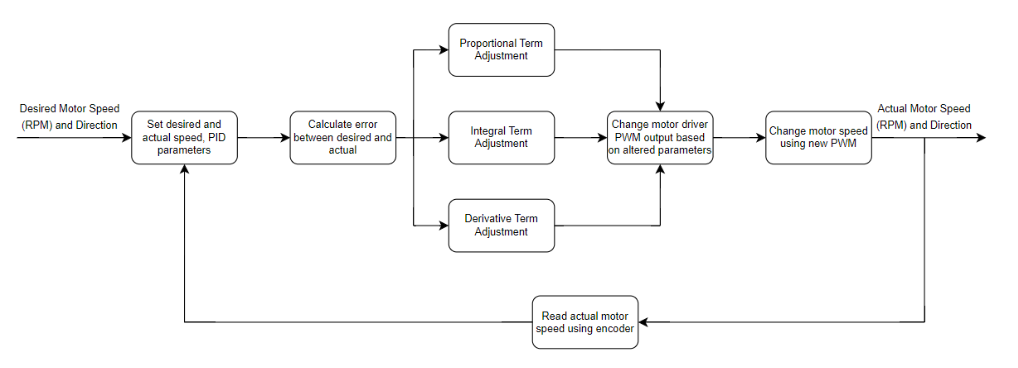
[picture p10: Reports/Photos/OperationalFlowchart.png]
OperationalFlowchart

The operations of this flowchart were informed by [5].

### Sorting and Collecting Operations - Overall Chart
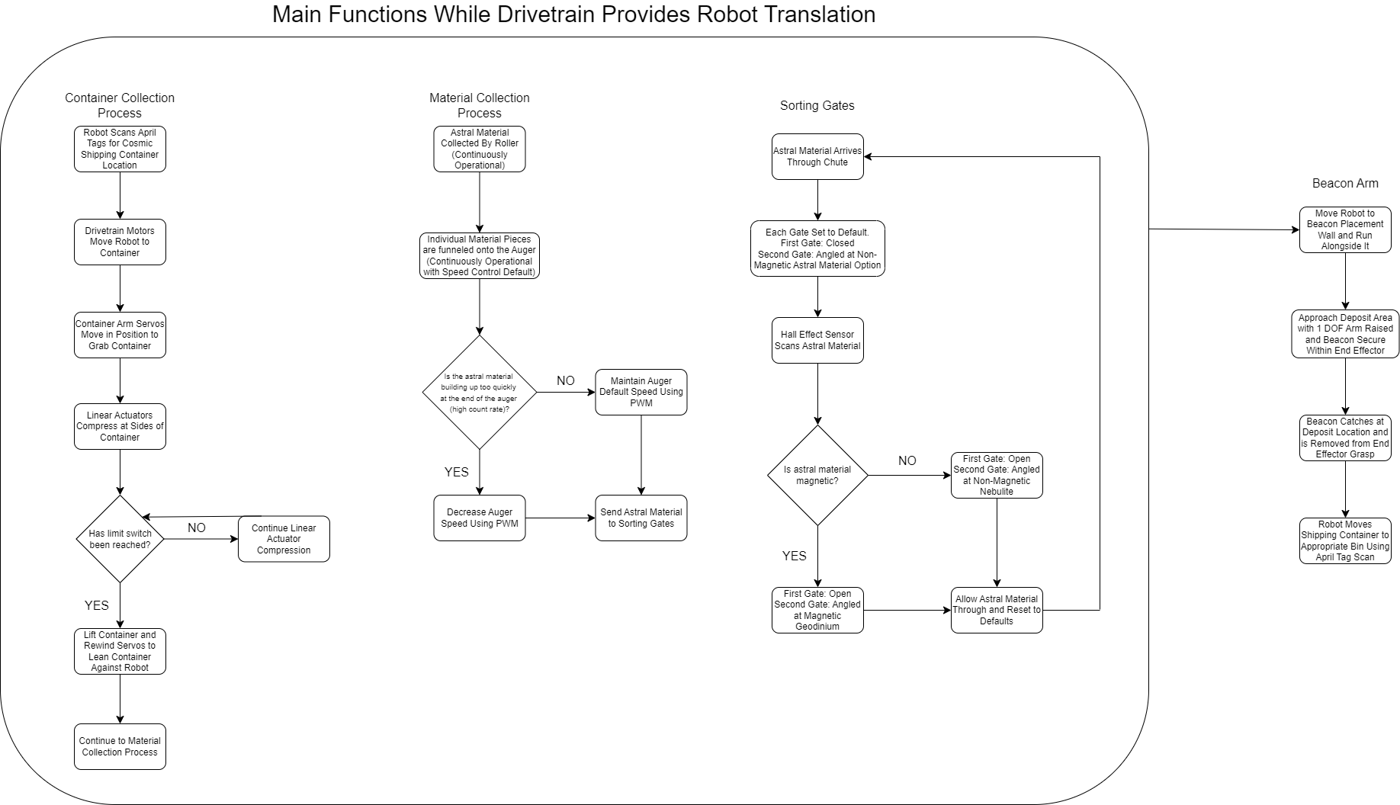
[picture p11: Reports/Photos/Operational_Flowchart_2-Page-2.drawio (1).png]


### Sorting and Collecting Operations - Individual Process Charts
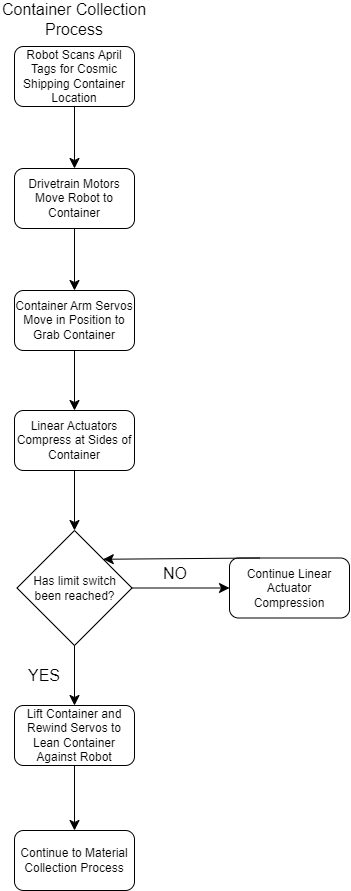
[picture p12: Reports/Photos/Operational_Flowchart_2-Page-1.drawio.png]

##
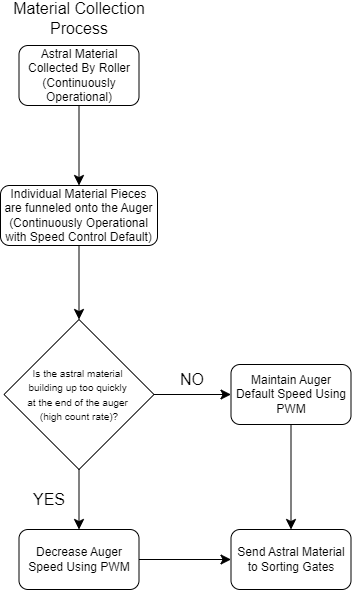
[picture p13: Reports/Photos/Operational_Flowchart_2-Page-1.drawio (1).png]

##
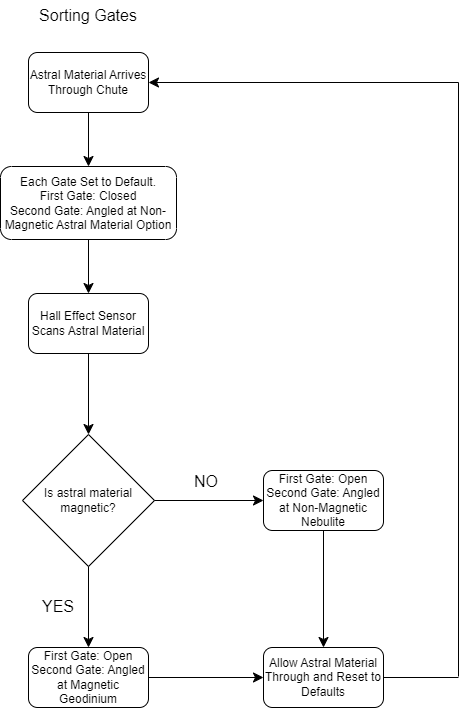
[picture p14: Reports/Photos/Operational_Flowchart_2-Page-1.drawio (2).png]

##
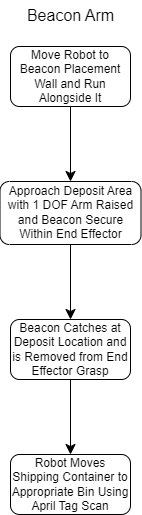
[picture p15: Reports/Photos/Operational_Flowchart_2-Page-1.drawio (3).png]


## BOM
Items with an asterisk (*Part Name) will be purchased by the Electrical Engineering Team. Other items will come from the Mechanical Team.

|Part|Manufacturer|Part Number|Distributor|Distributor Part Number|Quantity|Price per Item|url|
| :- | :- | :- | :- | :- | :- | :- | :- |
|12V 50:1 Metal DC Geared-Down Motor 37Dx70L mm, with 64 CPR Encoder |CQRobot |CQR37D12V64EN-F |Amazon |ASIN: B08ZK7KNJW |2 |$33.99 |https://www.amazon.com/CQRobot-Ocean-6V-3W-20RPM-40-oz-12V-6W-40RPM-70/dp/B08ZK7KNJW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|
|*Pololu Dual VNH5019 Motor Driver Shield for Arduino |Pololu |2507 |Pololu |N/A |1|$59.95 |https://www.pololu.com/product/2507|
|*Arduino Mega |Arduino |2152366 |Amazon |ASIN: ‎ B0046AMGW0 |1|$43.56 (Will borrow from lab) |https://www.amazon.com/ARDUINO-MEGA-2560-REV3-A000067/dp/B0046AMGW0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|
|9g Micro Servo Motor 10 pack (Sorting and Beacon) |Miuzei |N/A |Amazon |ASIN: B072V529YD |1 |$18.99 |https://www.amazon.com/Micro-Helicopter-Airplane-Remote-Control/dp/B072V529YD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|
|35kg Servo Motor (Lifting) |ZOSKAY |35 |Amazon |ASIN: B07S9XZYN2 |2 |$28.99 |https://www.amazon.com/ZOSKAY-Coreless-Digital-Stainless-arduino/dp/B07S9XZYN2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|
|High-Speed 0.6"/sec Linear Actuator 12v |Rtisgunpro |MN |Amazon |ASIN: ‎ B09X994MGX |2 |$18.99 |https://www.amazon.com/High-Speed-Actuator-actuators-Cabinets-Automation/dp/B09X994MGX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|
|Auger Greartisan DC 12V 200RPM Turbo Worm Geared Motor |Greartisan |JSX40-370 |Amazon |ASIN: B08K7HNXTM |1 |$14.99 |https://www.amazon.com/Greartisan-120RPM-Turbine-Reduction-JSX69-370/dp/B08K7HNXTM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|
|Greartisan DC 12V 200RPM Turbo Worm Geared Motor with Mounting Bracket |Greartisan |JSX40-370 |Amazon |ASIN: B0D1KCX2GX |1|$24.99 |https://www.amazon.com/Greartisan-200RPM-Geared-Mounting-Bracket/dp/B0D1KCX2GX|
|*4 PACK L298N Motor Drive Controller Board DC Dual H-Bridge |AITRIP |N/A |Amazon |ASIN: B07WS89781 |1|$9.99 |https://www.amazon.com/Controller-H-Bridge-Stepper-Control-Mega2560/dp/B07WS89781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|
|HiLetgo 10pcs Micro Limit Switch |HiLetgo |3-01-1546 |Amazon |ASIN: ‎ B07X142VGC |1|$5.99 |https://www.amazon.com/gp/product/B07X142VGC/ref=sw_img_1?smid=A30QSGOJR8LMXA&psc=1|
|2Pcs Thin Film Pressure Sensor |Walfront |Walfront9snmyvxw2|Amazon |ASIN: B07T1CHY58 |2|$9.78 |https://www.amazon.com/dp/B07T1CHY58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|
|*Electronics Kit Compatible with Arduino |ELEGOO |EL-CK-003 |Amazon |ASIN: B09YRJQRFF |1|$15.99 |https://www.amazon.com/ELEGOO-Electronics-Potentiometer-tie-Points-Breadboard/dp/B09YRJQRFF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|

## Analysis
### Wheel Speed
In order to verify that the robot would be able to fulfill the motor performance specifications, a series of calculations must be performed based on the motor characteristics and estimated wheel size. The first objective is to determine the wheel speed. It is assumed that the angular speed of the motor in RPM is equivalent to the angular wheel speed, as the given no-load speed accounts for the gear ratio of 50:1 internally. Wheel speed is calculated via the following equation [7]: 

$S=\pi \cdot D\cdot \left(\frac{RPM}{60\ s}\right)$

S=linear wheel speed, RPM=wheel rotations per minute, D=wheel diameter 

Based on the allotted 12x12 inch space and the estimated vertical space available from the base of the robot to the ground, the Mechanical Engineering team calculated that the wheels should at least have a diameter of 102 mm. The angular speed of the chosen motor is 200 RPM. This value and the wheel diameter in mm can be inserted into the equation for linear wheel speed, as done below: 

$S=\pi \cdot \left(102\ mm\right)\cdot \left(\frac{200\ RPM}{60\ s}\right)=1068.14\ \frac{mm}{s}=42.05\ \frac{in}{s}$
 
Using a linear wheel speed of 42.05 in/s, the time it takes to traverse the game field twice can be calculated, with one path being for collecting astral material and one for the return trip. If the result is within 3 minutes of gameplay, the request from Specification 3 is satisfied. The total area of the field is 93x45= 4185 square inches. Assuming the robot takes up the 12x12 inch starting floor space, one can divide the total area by 144 square inches to get the estimated number of square segments for the robot to move in, which would be about 29 segments. Accounting for a worst case path scenario would mean the robot would traverse every segment on the field twice, which would bring the value up to 58 segments. Moving from one segment to another would involve a displacement of 12 inches forward. The robot can move 42.05 in/s. Therefore, it would take 0.29 seconds (12 in / (42.05 in/s)) for the robot to translate a full segment. To find the total time it would take to traverse 58 segments, each with 12x12 square inches, multiply the time to traverse a full segment by the number of segments, which is demonstrated below:  

$\frac{0.29\ s}{1\ segment}\cdot 58\ segments=16.82\ s$

Therefore, the robot would take approximately 17 seconds at continuous speed operation to traverse the entire field twice, which is well under the 180 second timeframe. However, this is using the maximum, no-load speed, and there will be parts of the chosen path in which the robot is not constantly moving. Nevertheless, this serves as a good estimate for the worst case path scenario and allows more than enough time for stoppages during the match. The chosen motor subsystem satisfies the performance requests of Specification 3. 

### Torque and Maximum Power
Wheel speed is an important factor in understanding how qualified a motor is for satisfying specifications. However, torque is another characteristic that is important for when the robot will carry a heavy load. The relationship between speed and torque is inversely proportional. As motor speed increases, torque decreases, and vice versa [12]. The stall torque is representative of the state in which the motor is not rotating, having no angular speed. The given stall torque from the 50:1 DC Geared-Down Motor at 12V is 21 kg*cm or 2.06 N*m. When the torque is zero, the speed is at its maximum no-load speed, which as discussed previously is 200 RPM, or  20.94 rad/s, for this motor. Maximum power is equal to the product of half the no-load speed and half the stall torque [13]. Therefore, the following equation can be used to find the maximum power for the given motor: 

$P_{\max }=\left(\frac{2.06\ N\cdot m}{2}\right)\cdot \left(\frac{20.94\ \frac{rad}{s}}{2}\right)=10.78\ W$

The speed at a maximum power of 10.78 W will be half of the previously tested speed, but this state of the motor will provide more torque for a more realistic average load expectation. Calculating the new angular speed and the resulting time it would take to traverse the field twice is done below: 

$\frac{200\ RPM}{2}=100\ RPM$

$S=\pi \cdot \left(102\ mm\right)\cdot \left(\frac{100\ RPM}{60\ s}\right)=534.07\ \frac{mm}{s}=21.03\ \frac{in}{s}$

$\frac{12\ in}{21.03\ \frac{in}{s}}=0.57\ s$

$\frac{0.57\ s}{1\ segment}\cdot 58\ segments=33.06\ s$

As demonstrated through these calculations, when a balance of half the potential torque and half the potential speed is available, the robot still traverses the field twice in about 33 seconds.  

### Battery Life and Speed Relationship
In order to determine the longevity of the robot using the motor specifications, one must consider the number of matches that will be played and the battery usage per match. Game Manual 1 states that there will be three qualifying matches and three elimination rounds on the path to first place. It will be assumed that the robot is operating for a full three minutes in each and that the motors will be operating with a worst-case, heavy load current of 5.5A, the stall current. According to [15], the discharge time for a battery is equal to the estimated battery capacity in amp-hours divided by the current draw (amps) from the electrical load. The two motors are the electrical load in this case, each with a maximum 5.5A of current draw for a total of 11A. Six matches, at 3 minutes each, equals 18 minutes or 0.3 hours. Multiply this necessary discharge time of 0.3 hours by the 5.5A maximum to get the necessary battery capacity for the two motors, which equals 1.65 ah. This desired capacity is a small fraction of the available capacity for the 24V batteries being considered, with 100ah or more being a commonly used threshold. Therefore, the battery loss from round to round should not be an issue with regard to the motors. 

It is still important to consider the fact that the speed will drop as the available battery voltage decreases. If the voltage were reduced to 6V instead of the full 12V for the motors, the listed no-load speed would be 100 RPM, which would double the time estimate for the no-load, field segment calculations. Doubling the time estimate for the original no-load speed would result in 34 seconds, which meets Specification 3. Overall, the trend for the relationship between speed and voltage can be seen from [16], with the equation below: 

$RPM=V \cdot Kv\$

RPM=linear wheel speed, V=test voltage, Kv=(No-Load RPM / No-Load Voltage)

During testing, voltage to the motors can be measured using a multimeter, and the relative speed can be calculated using the test voltage and the process above. Exact voltage to speed data can then be extracted and used to make adjustments and assess what motor performance range is available. 

### PID Parameter Calculation  
As far as PID tuning is concerned for the Drivetrain motor control, the operational flow chart serves as a visual for how the closed-loop feedback control would look. The algorithm for the PID values is demonstrated here [14]:  

$u\left(t\right)=K\left(e\left(t\right)+\frac{1}{T_i}\int _0^te\left(\tau \right)d\tau +T_d\frac{de\left(t\right)}{dt}\right)$

The PID control loop will be represented using Arduino, with parameters for the proportional, integral, and derivative values being inputs that can change based on experimental feedback. For example, if one starts with just proportional control, the output will oscillate and settle with a significant steady state error. Adding a constant for integral control would help correct the steady state error but add to the settling time. Adding a constant for derivative control would reduce the settling time, which would result in full PID control, the best combination of tools available for adjusting the reaction of the robot as it targets the desired motor speed.  

## Execution Plan

In order to accomplish the design objectives for the motor control subsystem, the designated member of the Electrical Engineering Team in charge of motor control will coordinate with the Mechanical Engineering Team to implement the functionality required to run the physical mechanisms of the robot. The work will overlap with the purpose of the mechanisms, but the Electrical Engineering work will focus on the software and circuit skills necessary to address the purpose, while the Mechanical Engineering Team will focus on the construction of the mechanisms themselves. PID control for the drivetrain motors will be implemented using Arduino software, with live testing being the most realistic option for knowing how to adjust the PID parameters to their most ideal state. The initial software for PID control and for the other mechanisms will be written and ready to test by early February, with physical construction of the mechanisms proceeding alongside the software development. Towards the end of the prototyping period in late February, the motor circuits will be constructed, based on the schematics present in the Detailed Design report. During debugging, which will last from late February to the middle of March, motor command logic will be adjusted based on testing, with parameter adjustment being the focus for PID control and positional changes being the focus for servo mechanisms. For example, any position-based commands for the Beacon Arm may need slight corrections based on the resulting placement location on the field. A model of the field will be constructed using the CAD designs given in the Game Manuals in order to replicate the match conditions as closely as possible. 

## References
1.	“Motor Driver Fundamentals: Your Guide To Efficient Motor Control - Jhdpcb,” jhdpcb, 	Jan. 18, 2024. https://jhdpcb.com/blog/efficient-motor-control/#:~:text=The%20key%20role%20of%20the,enable%20speed%20and%20torque%20control 
2.	E. P. Company, “Motor Encoders: What is a Motor Encoder? How Do Motor Encoders 	Work?,” www.encoder.com. 							https://www.encoder.com/motorencoders#:~:text=What%20are%20motor%20encoders%3F,are%20either%20incremental%20or%20absolute 
‌
3.	Safety of machinery - Electrical equipment of machines. 2016. Available: 			https://webstore.iec.ch/en/publication/26037 
4.	Sparkfun, “Servos Explained - SparkFun Electronics,” www.sparkfun.com. 		https://www.sparkfun.com/servos 
5.	“PID CONTROLLER Archives - The Engineering Concepts,” The Engineering Concepts, 	2018. https://www.theengineeringconcepts.com/tag/pid-controller/ (accessed Nov. 26, 	2024). 
6.	F. Zhang, “How Does Limit Switch Feedback Work in Actuators,” Progressive 		Automations, Mar.18, 2021. https://www.progressiveautomations.com/blogs/how-to/how-	does-limit-switch-feedback-work-in-actuators (accessed Nov. 26, 2024). 
7.	“Wheel Speed Calculator,” Calculator Academy. https://calculator.academy/wheel-	speed-	calculator/ 
8.	“In-Depth: Interface L298N DC Motor Driver Module with Arduino,” Last Minute 		Engineers, Nov.28, 2018. https://lastminuteengineers.com/l298n-dc-stepper-driver-	arduino-tutorial/#google_vignette 
9.	N. Bong, “Components of an Electric Linear Actuator,” Progressive Automations, Oct. 	26, 2021. https://www.progressiveautomations.com/blogs/products/inside-an-electric-	linear-actuator?srsltid=AfmBOopJH-								4XrJ9V0OS1Lk9yvIklYkLR6PysyYtZrjL_aBocRBR64l8M (accessed Nov. 26, 2024). 
10.	“3-pin pressure sensor,” Arduino Forum, Jul. 24, 2018. https://forum.arduino.cc/t/3-pin-	pressure-sensor/538150 
11.	“Arduino - Limit Switch | Arduino Tutorial,” Arduino Getting Started. 			https://arduinogetstarted.com/tutorials/arduino-limit-switch 
12.	“Speed vs Torque,” Power Electric. https://www.powerelectric.com/motor-blog/speed-vs-	torque 
13.	“Motor Calculations Calculating Mechanical Power Requirements.” Available: 	https://pages.mtu.edu/~wjendres/ProductRealization1Course/DC_Motor_Calculations.pdf 
14.	K. J. Astrom, “PID Control,” 2002. Available: 						https://www.cds.caltech.edu/~murray/courses/cds101/fa02/caltech/astrom-ch6.pdf
15. D. Power, “How To Calculate Battery Run Time,” Lithium ion Battery Manufacturer and Supplier in China-DNK Power. https://www.dnkpower.com/how-to-calculate-battery-run-time/
‌
16. “Voltage To Rpm Calculator - Calculator Academy,” Calculator Academy, Feb. 2024. https://calculator.academy/voltage-to-rpm-calculator/ (accessed Nov. 30, 2024).
17. A. Rouse, “The Different Types of Braking in a DC Motor,” AMBI-Tech Brakes, Oct. 08, 2020. 	https://www.ambitechbrakes.com/the-different-types-of-braking-in-a-dc-motor/

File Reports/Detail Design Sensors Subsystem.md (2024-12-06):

# Sensors Subsystem Detail Design
## Function of the Subsystem
The goal of this subsystem is to be able to provide information to the robot for multiple different types of data.
The information needed to provide includes position of the robot, number of materials collected, number of materials deposited, state of start LED, and whether the collected material is magnetic or not.

The position data is provided as feedback to the navigation control.
The number of materials provides information to the sorting control.
The type of material provides information to the chute control.
The state of the start LED provides information on whether the robot should start or not.
The start LED will provide the start signal to the main controller, which is a Jetson Nano.

For each separate sensor, noise needs to be accounted for, and calibrations have to be set.
The noise and calibration will be acted on before it is sent to a higher controller.
Each sensor needs its information to be properly directed and processed.
The information needs to be in a format that is easily transferable and easy to act on.
For the sensors that need sensor fusion, this will be done before the data is sent to a higher controller.
 
## Specifications and Constraints
Specifications:
1.	The robot's distance measurement sensor shall be able to find the walls of the game field and the cave.
2.	The robot's light detector shall be able to detect when the start LED turns on.
3.	The robot's magnetic sensors shall be able to detect the magnetic fields of the Geodinium.
4.	All of the robot's sensors shall be able to work effectively despite background interference in the competition environment.

Constraints:
1.	The robot shall be able to count the number of materials collected and deposited.
2.	The robot shall know its current position.
3.	The distance sensor shall detect a maximum of 8 ft, or 2.4 m.
4.	The magnetic sensor shall provide a signal that is larger than the resolution of the Arduino's Analog-to-Digital Converter.
5.	The light detector shall provide a signal visible through the background noise.
7.	The robot's general sensor subsystem shall have a user manual that explains functionality and design intent.

## Overview of Proposed Solution
To meet the listed specifications and constraints, a suite of sensors is composed to solve each of the problems individually.
This suite includes a Light Detection and Ranging device (LiDAR), photoresistors, Hall Effect sensors, and an Inertial Measurement Unit (IMU).
The LiDAR provides direct feedback for position.
It will provide the distance between the robot and the walls of the arena.
This meets specification 1 and helps with constraint 2.
The Hall Effect sensors will be used to detect the magnetic field from the magnetic materials.
This meets specification 3.
The IMU will be used to get position and will be the main solution for constraint 2.
The photoresistors will be used to detect the presence of light.
One photoresistor will be used to detect when the start LED has turned on.
This meets specification 2.
The other photoresistors will be used with their own LEDs to count the number of materials.
This meets constraint 1.
For specification 4, the sensors most prone to noise from the environment will be the photoresistors.
They will need to be properly calibrated to make sure that they do not send a signal when they are not supposed to.

## Interface with Other Subsystems
The IMU and LiDAR will provide positional feedback to the navigation control.
The photoresistor for the start LED will turn on the robot so that it can start completing its goals.
This will require activating the controllers, so that they can start running their scripts.
Each of the controllers will then properly set up and begin running the other subsystems.
The photoresistors for counting materials and the Hall Effect sensors will send information to the lower-level controller, which is an Arduino Mega.
This set of sensors will inform the controller about where the materials should be sent.

## Buildable Schematic
Sensors Subsystem Schematic

## Operational Flowchart
Sensors Subsystem Operational Flowchart

## Analysis
### LiDAR
LiDAR’s implementation has a few options that would each meet our specifications.
First, if LiDAR is continuously used to get position feedback, it can be incorporated through Kalman Filters to provide higher resolution of the current position than any single sensor.
However, this option will require more time for developing than any other option [1-2].
Second, if LiDAR is checked on specific time intervals, this position data could be compared with the current position data.
If the two differ, then a correction can be made.
Third, if LiDAR is checked when an error arises, it can be used to find the current position.
Errors that could trigger the LiDAR include motors not moving the robot, such as from running into something or the IMU not reading a change in position when it should be.
This implementation requires the least work for the LiDAR, but proper flags need to be put in place for edge cases.

The current LiDAR picked out for this project is the Garmin LIDAR-Lite v4 LED.
It outputs data with 3.3V GPIO pins.
The Jetson Nano has 3.3V GPIO pins while the Arduino Mega has 5V pins, so it will be read by the Jetson Nano.
The LiDAR has a Field-of-View of 4.77 degrees.
It has a minimum distance of 5 cm and a maximum of 10 m.
Over I2C connection, it has a refresh rate of at least 200 Hz and a maximum of 400 kHz.
At best the error is +/- 1 cm and at worst +/- 5 cm.
The best case is at 2 m, and the worst case is at 10 m.
This specific LiDAR works best because it has a much smaller than average minimum distance.
The maximum at 10 m is more than enough given the farthest distance the robot would read would be 8 ft, or 2.44 m.
This LiDAR also has an onboard microprocessor that averages multiple readings and removes some noise, and it is directly connectable to the robot with standard integration [3-4].

### Photoresistor
Photoresistors will be used for two different problems.
The first issue is to detect the starting LED.
This is solved by using a photoresistor connected between 5 V and an Arduino digital interrupt pin.
When enough light is incident on the photoresistor, it will pull the digital pin high.
The photoresistor will be placed as close as possible to the start LED, so its resistance will be made very low when the LED turns on.
An interrupt pin can be used to turn the Arduino on or to wake it from sleep mode.
The Arduino Mega has 6 dedicated interrupt pins, digital pins that can be tied to interrupts, and analog pins that can be tied to interrupts [5].

The second issue is to count the materials.
They must be counted when entering and exiting the auger, or whether a material has been collected and when it has been deposited.
Keeping track of the materials allows the robot to know when to change the deposit location.
The robot has one auger that deposits into a chute with a lever to designate where the material should go.
When the material exits the chute, it will fall onto a gate that will have a photoresistor that will trigger so the Hall Effect sensors can determine if it is magnetic or not.
To implement the counters, a photoresistor will be placed across from an LED.
The materials will travel between the photoresistor and LED.
Like the start LED sensor, these photoresistors will be at digital high when there is no material and then be at digital low for a moment when a material passes between the photoresistor and LED.
This digital low can be used to count the materials.

The GL125 series photoresistors will be used for their robustness and straightforward application.
They have a maximum voltage of 250 V, much larger than anything the robot will be using.
The photoresistors have a peak response to green light, so a green LED will be used for each of the counting photoresistors.
It has a monomial response that is easily calibrated with software or hardware.
Calibration will be necessary to remove the noise from the environment [6].

### Hall Effect Sensor
There are two different materials that will be collected by the robot.
One of the materials produces a magnetic field, while the other does not.
Hall Effect sensors can be used to detect the magnetic field produced by the magnetic materials.
The materials will be deposited on a gate to be measured.
While on this gate, three Hall Effect sensors will be placed along three different orthogonal axes.
The photoresistor will trigger the Hall Effect sensors to be read by the Arduino analog pins.
If any sensor is above a certain software threshold, it will trigger the lever.
Whether the sensors read a magnetic field or not, the material will be dropped after a set amount of time to its container.

The AH49E is a Hall Effect device that has a linear response to magnetic fields.
The input voltage determines the slope, or resolution, of the sensor.
The sensor output half of the input voltage when no magnetic field is present, and it either outputs a higher or lower voltage depending on whether it detects a positive or negative magnetic field.
Each sensor can only detect in one dimension, perpendicular to the flattest side of the device.
Therefore, the robot will need three sensors to detect the three different axes, since the material can be orientated in any direction.
The input voltage has a maximum of 8 V.
5 V will be used, since it is available and the maximum that can be measured by the Arduino [7].

### IMU
The IMU provides valuable feedback to the motor control.
As the robot moves, it could become offset from where it thinks it is.
It is the goal of the IMU to correct this action.
The IMU will provide acceleration and orientation data, through its accelerometer and gyroscope.
The acceleration data will be integrated twice to get position and added to previous position.
This can create detrimental levels of drift and will be accounted for through sensor fusion [8].

The SparkFun Optical Tracking Odometry Sensor (OTOS) incorporates an IMU and an optical velocity sensor to provide positional feedback.
The optical velocity sensor is the same as the one found in a computer mouse.
OTOS comes with its own on-board processor that implements a Kalman Filter between the two sensors and to judge the effectiveness of both.
It also comes with a calibration table to give the sensor a linear offset that is much easier to calibrate than a non-linear offset.
The linear offsets can be measured and input once and stored on the robot, as they will be consistent.
It does not need to move for about 0.5 seconds each time it is turned on to calibrate the gyroscope.
The sensor provides information every 3 ms.
It outputs a digital high when it is ready to send data to help with asynchronous timing.
It is powered with 3.3 V and uses 3.3 V GPIO.
It connects over I2C and will connect directly to the Jetson Nano.
It will need to be on an I2C bus, given that the LiDAR is also connected.
Code is provided to start collecting data as soon as the sensor has been connected [9-10].

## Sensor Characteristics
|Sensor|Sensing Range|Interface|Typical Voltage|Typical Current|
| :- | :- | :- | :- | :- |
|LiDAR|0.5 m to 10 m|3.3 V I2C|5 V|85 mA|
|Photoresistor|1 Lux to 100 Lux|Analog|5 V|Depends on incident light|
|Hall Effect|-1000 to +1000 Gauss|Analog|5 V|3.5 mA|
|IMU|-2.5 m/s to +2.5 m/s|3.3 V I2C|3.3 V|1 mA|

## Ethics
The Sensor Subsystem uses multiple devices that have been developed by outside sources.
These sources will be properly accredited to recognize the work that was put into this project.
Out of the sensors listed, the LiDAR and OTOS both have lights.
The LiDAR uses an infrared LED that is invisible and completely safe to the human eye [3].
The OTOS has a chip that produces an infrared Class I Laser [11].
A Class I Laser is completely safe as well [12].
The rest of the sensors follow the rules and will be properly attached to the robot to prevent any hazards.
The Sensor Subsystem will also have a user manual to help future students understand how the Sensor Subsystem operated.
The user manual will provide valuable information for students trying to reproduce or build on the present design.

## Bill of Materials
|Item|Unit Price|Quantity|Total Price|URL|
| :- | :- | :- | :- | :- |
|LiDAR|$81.25|3|$243.75|https://www.mouser.com/ProductDetail/SparkFun/SEN-18009?qs=iLbezkQI%252BsjpCIKpfdq6BA%3D%3D|
|Qwiic Connector Set|$9.99|1|$9.99|https://www.amazon.com/elechawk-SparkFun-Development-Breadboard-Connector/dp/B08HQ1VSVL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|
|4-port Qwiic I2C Bus|$6.50|2|$13.00|https://www.amazon.com/SparkFun-MultiPort-connectors-Alternative-configuration/dp/B09M9BX55S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|
|Photoresistor|$16.49|1|$16.49|https://www.amazon.com/Juried-Engineering-Photoresistor-GL12528-Sensitive/dp/B08F3WPNPF|
|Green LED|$0.311|2|$0.622|https://www.newark.com/led-technology/l02r5000q1/led-green-t-1-3-4-5mm-3-7mcd-567nm/dp/97K4041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|pcrid||plid||kword||match|e|slid||product|97K4041|pgrid|1231453304461926|ptaid|pla-4580565455222458:aud-807872783|&msclkid=9dbbf8c3c12e198d33ec9f87232c30e8|
|Hall Effect Sensor|$0.48|3|$1.44|https://www.mouser.com/ProductDetail/Diodes-Incorporated/AH49FZ3-G1?qs=dZoB6MK9LKPUjOBJDQRw%2FA%3D%3D|
|Solderful Breadboard|$2.49|1|$2.49|https://www.digikey.com/en/products/detail/digikey/DKS-SOLDERBREAD-01/21274484|
|OTOS|$79.95|1|$79.95|https://www.amazon.com/SparkFun-Optical-Tracking-Odometry-Sensor/dp/B0D6LQGBSK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|
|Total|||$367.732|

## Works Cited
1.	G. Welch, G. Bishop. “An Introduction to the Kalman Filter.” mit.edu. Mar. 2002. Accessed: Nov. 2024. [Online]. Available: https://www.mit.edu/course/16/16.070/www/project/PF_kalman_intro.pdf
2.	“How a Kalman filter works, in pictures.” bzarg.com. Apr. 2015. Accessed: Nov. 2024. [Online]. Available: https://www.bzarg.com/p/how-a-kalman-filter-works-in-pictures/ 
3.	“LIDAR-Lite v4 LED.” garmin.com. Accessed: Nov. 2024. [Online]. Available: https://www.garmin.com/en-US/p/610275#specs
4.	“LIDAR-LITE V4 LED: OPERATION MANUAL AND TECHNICAL SPECIFICATIONS.” garmin.com. Sep. 2020. Accessed: Nov. 2024. [Online]. Available: https://static.garmin.com/pumac/LIDAR-Lite%20LED%20v4%20Instructions_EN-US.pdf
5.	“Arduino® Mega 2560 Rev3: Product Reference Manual.” arduino.cc. Nov. 2024. Accessed: Nov. 2024. [Online]. Available: https://docs.arduino.cc/resources/datasheets/A000067-datasheet.pdf
6.	“GL125 Series Photoresistor.” know-tech.com. Accessed: Nov. 2024. [Online]. Available: https://knowing-tech.com/wp-content/uploads/data/g/GL12528.pdf
7.	“LINEAR HALL-EFFECT IC : AH49E.” digikey.com. Rev. 1.3, Aug. 2010. Accessed: Nov. 2024. [Online]. Available: https://www.digikey.com/htmldatasheets/production/1364519/0/0/1/ah49e.html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
8.	“LSM6DSO: Datasheet.” st.com. Rev. 3, Jun. 2024. Accessed: Nov. 2024. [Online]. Available: https://www.st.com/resource/en/datasheet/lsm6dso.pdf
9.	loricrotser. “SparkFun Optical Tracking Odometry Sensor - PAA5160E1 (Qwiic) Hookup Guide.” sparkfun.com. Nov. 2024. Accessed: Nov. 2024. [Online]. Available: https://docs.sparkfun.com/SparkFun_Optical_Tracking_Odometry_Sensor/introduction/
10.	“SparkFun_Optical_Tracking_Odometry_Sensor.” github.com. Nov. 2024. Accessed: Nov. 2024. [Online]. Available: https://github.com/sparkfun/SparkFun_Optical_Tracking_Odometry_Sensor
11.	“PAA5160E1-Q: Optical Tracking Chip.” sparkfun.com. Ver. 0.8, Sep. 2022. Accessed: Nov. 2024. [Online]. Available: https://cdn.sparkfun.com/assets/c/6/8/0/5/PAA5160_Datasheet_General.pdf
12.	J. Maltais. “Class 1 Laser Products: Regulations Explained.” laserax.com. Aug. 2021. Accessed: Nov. 2024. [Online]. Available: https://www.laserax.com/blog/class-1-laser-products-regulations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,a%20%E2%80%9CClass%201%20laser%20product%E2%80%9D%20label%20are%20safe

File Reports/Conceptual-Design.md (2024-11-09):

# Conceptual Design
## Introduction
The Institute of Electrical and Electronics Engineers (IEEE) hosts a yearly hardware competition at its Southeast Conference (SECON) for students to compete in. Tennessee Technological University has competed in the IEEE SECON hardware competition in the past but has often had issues undiscovered until the actual competition. The aim of this project is to design and build a robust, consistent robot to place as highly as possible. 

### Restatement of Problem and Scope:
The 2025 competition rules and limitations will be listed in the specifications section below but, in short, its challenge takes place over 3 minutes and involves collecting and separating two types of 40mm icosahedrons (astral material) randomly distributed on the field. Geodinium, one type of astral material, is slightly magnetic and heavier than Nebulite, the other type. The challenge is to sort these two types of astral material into two designated containers, and then bring those containers to a randomly chosen area on the board. Additionally, there is a dark roofed “cave” area with further Geodinium and Nebulite. The board is relatively simple with few obstacles beyond the containers and astral materials to navigate around, and as such, the goal is to focus on reliability followed by an extensive testing period. There are two types of matches, qualification matches in which the eight teams with the highest scoring qualification matches, and elimination matches where two teams directly compete against each other’s scores [1].

Time is the major limiting factor as the competition takes place early into the second semester of this capstone project. By following an accelerated design and build schedule, this limits the design and testing periods for this project. The point distribution greatly rewards being able to correctly and reliably sort Geodinium and Nebulite into their corresponding containers. By implementing a camera for computer vision purposes and a heavy emphasis on testing, the robot can reliably gain the astral material points and unreliably gain others (such as for placing a beacon into a designated position), performance can be optimized for both the qualification matches and elimination matches [1].
## Restate Shall/May Statements
### Specifications
1)	The robot shall act autonomously. Rule G08 [2].
1)	The team shall design a robot to earn as many points as possible [2].
    1)	The robot may score 5 points by moving out of the landing pad [2].
    1)	The robot may score 5 points by moving out of the landing pad within 3 seconds of the Start LED [2].
    1)	The robot may score 15 points by moving into the cave [2].
    1)	The team may score 5 points by entering the Promotional Design Competition [2].
    1)	The robot may score 60 points for putting both containers in the correct zone [2].
    1)	The robot may score 34 points by completely supporting all Astral Material [2].
    1)	The robot may score 80 points by putting all Nebulite in its container [2].
    1)	The robot may score 108 points by putting all Geodinium in its container [2].
    1)	The robot may score 40 points for putting the Team Beacon in the Beacon Mast [2].
1)	The robot shall fit within a cube with 12 inches per side at the start of the match. Rule G04 [2].
1)	The robot shall be able to detect the walls of the arena, walls of the cave, and cave entrance. Rule S03 states that if the robot causes field damage, the team will be penalized. Detecting walls stops the robot from causing damage by moving into it [2].
1)	The robot shall stay on the game field. Rule S01 [2].
1)	The robot may have a single, simple electrical start button that shall be clearly labelled. The operation of this button shall prevent the robot from moving for five seconds. Rule R03 [1].
1)	The robot shall have a clearly labelled emergency stop button that immediately halts all functions safely and quickly. Rule R05 [1].
1)	The robot shall have a source of identification clearly associating it with Tennessee Technological University. Rule R10 [1].
1)	The robot may use light sources that shall not strobe, be excessively bright, or pose safety issues. Rule R17 [1].
1)	The robot shall cease operation of all its units after the allotted 3-minute timeframe of play is over, and no game element positions can be disturbed after time expires. Rule G07 [2]. 
1)	The robot shall account for background interference in the competition environment. Rule R13 [1].
1)	The robot shall sustain power of 30V maximum. Rule R16 [1].
	
### Constraints
1)	The robot shall read April Tags to help with Specifications 1, 2-v, 2-vii, 2-viii, and 2-ix. 
1)	The robot shall have a user manual that explains functionality and design intent for each subsystem.
1)	The robot shall adhere to applicable requirements in standard IEC 60204-1 pertaining to electrical supply, electromagnetic compatibility, emergency stop, and control circuit protection. The power-based and electromagnetic interactions of components in the motor control subsystem will need to adhere to this standard [3].

## High-Level Solution

### Camera

The camera will be the robot's primary means of object detection, and will also help with line detection. The camera will send its depth and image input to the microprocessor where the input will be filtered to a usable state, while that is happening the other inputs from general sensors will also be fed to the microcoprocessor and each input will be filtered to obtain a usable input. After usable inputs are obtained the sensor and camera inputs will be be put into object and line detection algorithms, which will localize the astral material, game field and cave walls, lines, and shipping containers on the robot's inner grid system. All this information will then be processed and sent to navigation and master control. 

### General Sensors

A suite of sensor will be used for this project.
A sensor is needed to detect the lines on the ground, difference between the two materials, the LED to start the robot, and the current location of the robot.
The line sensor will need to detect the difference between the black ground and the white lines.
This will need to be used when the robot is entering and exiting the cave to make sure it is properly aligned.
The start LED sensor will need to detect the LED that starts the robot at the beginning of the match.
The start LED will have a single task of sending a signal once a LED lights up, informing the robot to begin operations.
The location sensor will need to know where the robot is.
The location of the robot will be continuously updated as the robot traverses the field.
The location sensor will use sensor fusion in order to minimize drift found in most sensors used to navigate.

All sensors will send their data to the Jetson Nano for processing and interpretation.
Data will be filtered and compared for sensor fusion for the location sensor.
For the sensors that rely solely on their own information, they will be filtered and then used as inputs to help navigate and run the robot.
All sensors will help in making sure the robot acts autonomously.

### Navigation and Master Control

The Jetson Nano functions as the hub for the both navigation algorithms and master control functions. In short, it will take sensor data from the camera and general sensors, work with these systems to localize the robot to a specific position on an internal grid, and then utilize an algorithm to find a path that will achieve the robot's objectives within the given time frame. The minimum functioning product of this subsystem will be able to, given mostly accurate sensor data, reliably navigate the robot to pick up a maximum amount of astral material within the given time frame and with few mistakes. The ideal functioning product of this subsystem will be able to reliably navigate the robot to pick up all the astral material, and finish all other objectives within the time frame with no mistakes, even given fuzzy sensor data.

### Motor Control

The motor control subsystem for robot movement functions as the feedback-based reaction center for the robot’s processes. It uses the input taken in from sensory data, such as object and line detection or map navigation, and follows the commands given to it from the master control to perform the physical responses of the robot. Motor control can include the following components: a microcontroller (MC), motor, motor driver, encoder, power supply, and specific components for noise reduction and circuit protection [1]. The motor microcontroller carries the digital signal commands for the designated motor to operate as required. However, the power that the MC needs to function is not enough in comparison to what the motor needs. Therefore, it is essential to have a component that can step up the power for the motor while still using the MC for commands. This is the purpose of the motor driver. The motor microcontroller sends a digital signal to the driver using PWM to set the desired motor speed. Encoders that detect the motor shaft speed/position to provide the actual speed of the motors are useful for completing a closed loop feedback system, such as with PID control [2]. All logic control circuitry, which includes the master control and encoders, will receive low voltage from the power subsystem, while the motor driver will receive high voltage in order to provide the high power needs of the motors. 

Several types of motors are utilized in the solution. Brushed DC motors are used for the mechanisms that have continuous feedback based on desired versus actual motor speed, such as with the overall robot movement and the collection of astral material. Separate motor drivers are connected to these motors and provide the appropriate power based on PWM input from the microcontroller. Linear actuators will be used for clamping onto the shipping container, and they will need drivers as well for directional control of the extension of the actuator. Servo motors will be used for the material sorting mechanism via a system of gates, lifting the shipping container, and controlling the positioning of an arm that will place the Team Beacon. Servo motors are useful for precise positioning and may not need an external driver as the control circuit is integrated into the motor [32,33].

### Power Management

The LiFePO4 battery will be sufficient for the power subsystem requirements. These batteries will consistently and continuously power all required electrical components within the allotted time frame or until the E-stop button is pressed. The microcontroller, motors, and most sensors will all be driven by this subsystem. Once the circuit is closed, the robot will wait for the Start LED sensor to begin its mission. This subsystem must be tested as fully operational and consistent in order for the robot to meet all specifications and constraints.

### Hardware Block Diagram
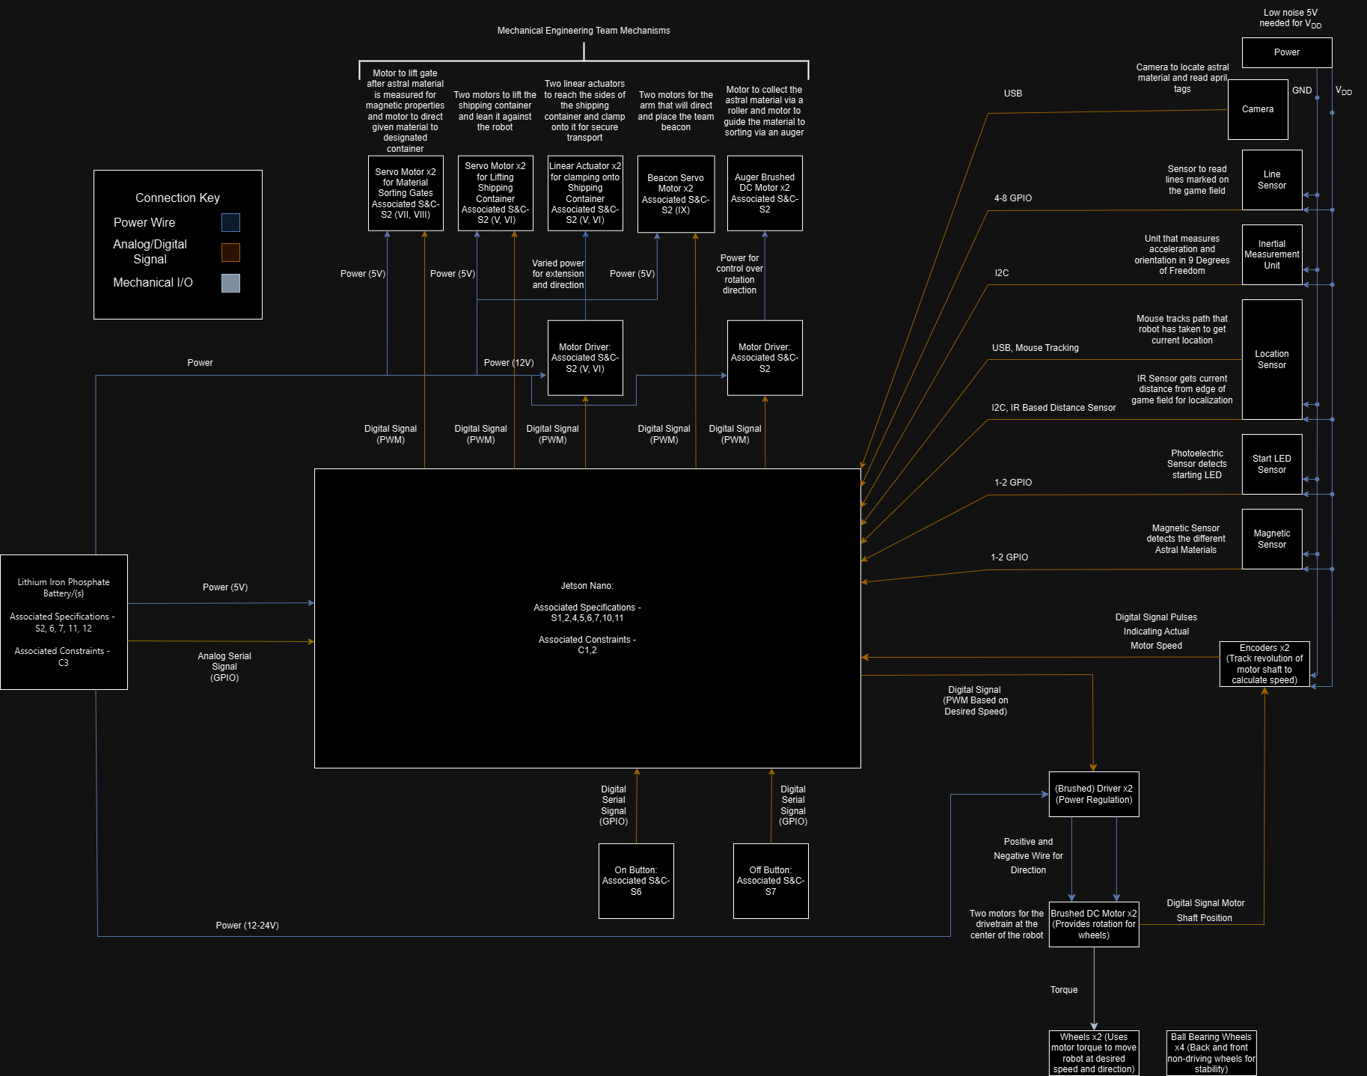
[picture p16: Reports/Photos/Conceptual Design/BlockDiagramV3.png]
Hardware Block Diagram

### Operational Flowchart
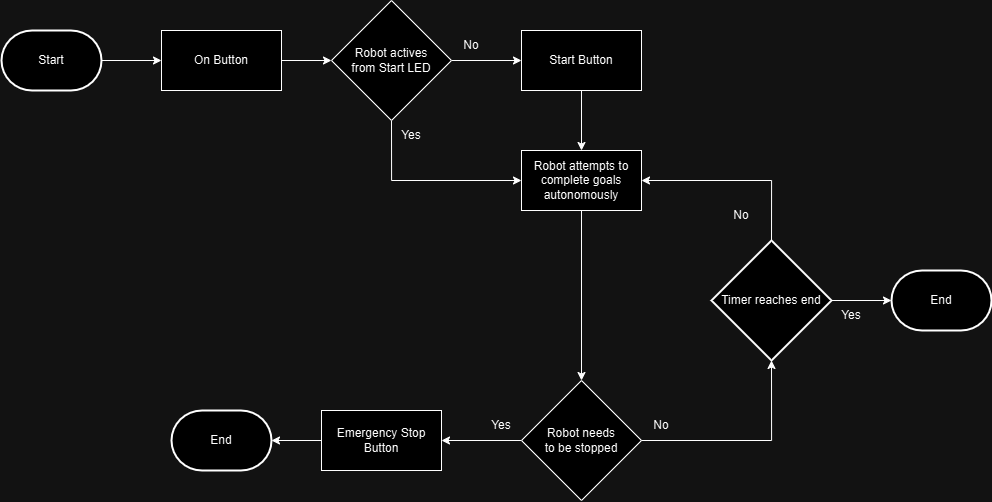
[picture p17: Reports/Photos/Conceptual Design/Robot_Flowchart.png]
Operational Flowchart

### High Level Robot Autonomous Operation Flowchart
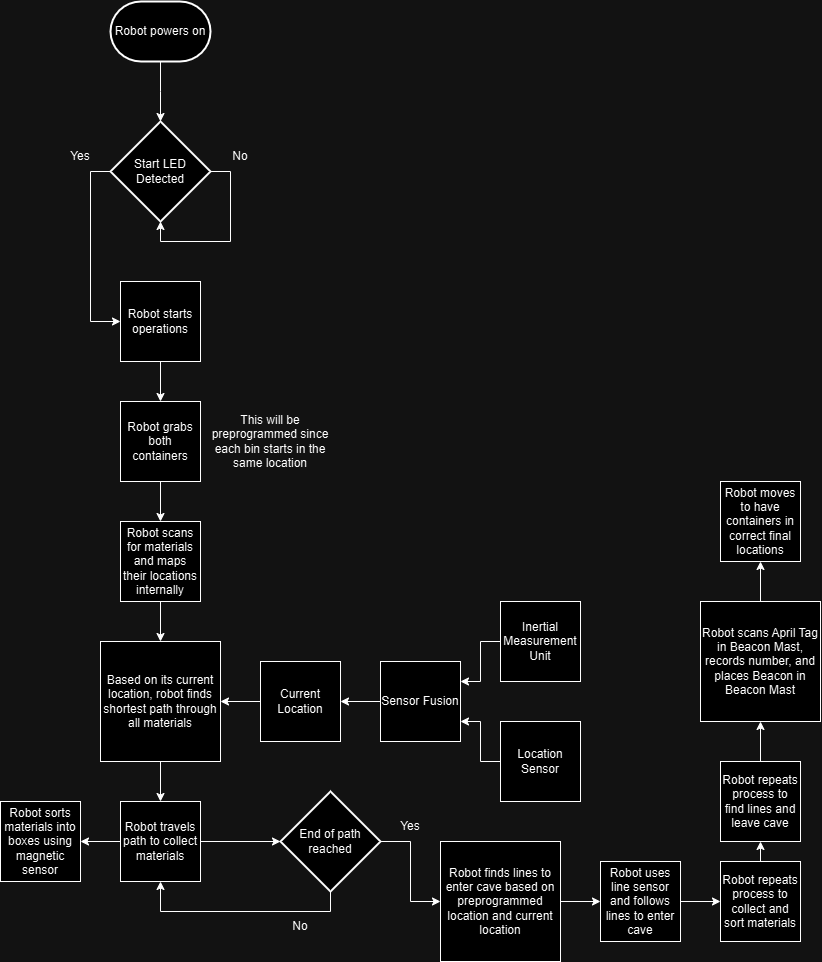
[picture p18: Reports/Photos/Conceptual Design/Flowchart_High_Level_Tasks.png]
High Level Robot Autonomous Operation


## Subsystems
### Camera
Customer: Dakota Moye

Designer: Sam Hunter

#### Atomic Subsystem Specifications

1. The robot shall act autonomously [S1].
2. The camera shall detect the Nebulite [S2-vii].
3. The camera shall detect the Geodinium [S2-viii].
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

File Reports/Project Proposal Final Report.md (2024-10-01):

## Intro

The Institute of Electrical and Electronics Engineers (IEEE) hosts a yearly hardware competition at its Southeast Conference (SECON) for students to compete in.  Tennessee Technological University has competed in the IEEE SECON hardware competition in the past but has often had issues undiscovered until the actual competition.
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

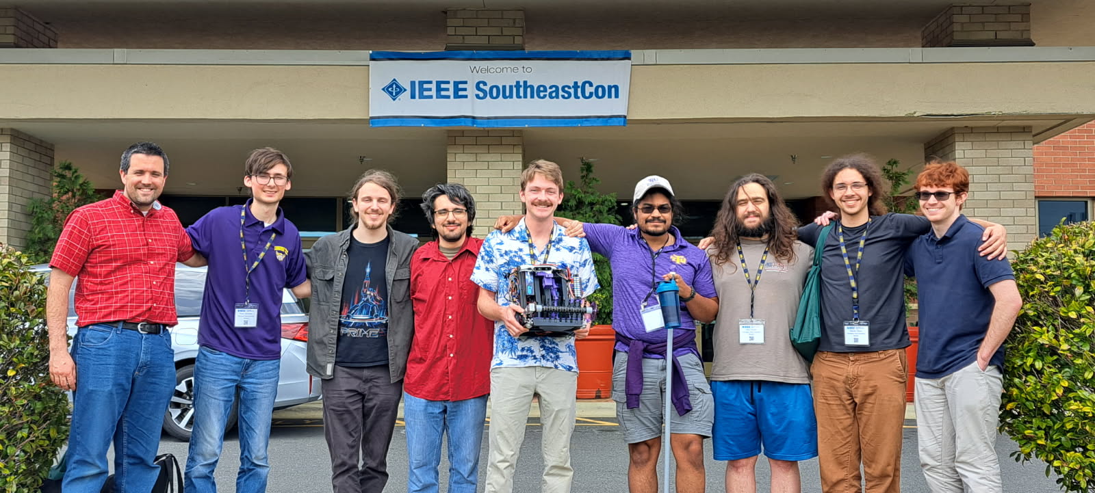
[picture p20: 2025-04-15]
Reports/Final Design Poster/Team Picture SECON 2025.jpg

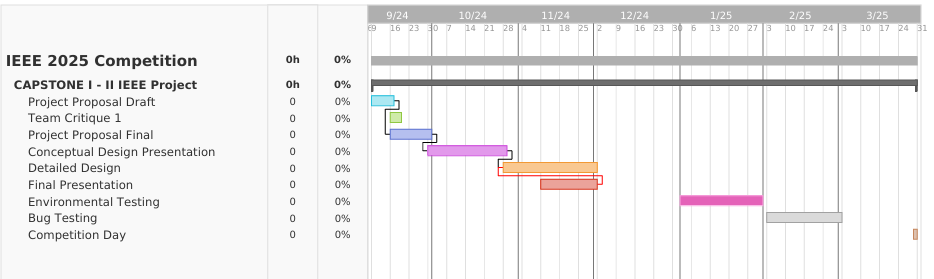
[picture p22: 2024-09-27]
Reports/Images and Sources/Project Proposal/Screenshot 2024-09-27 141156.png

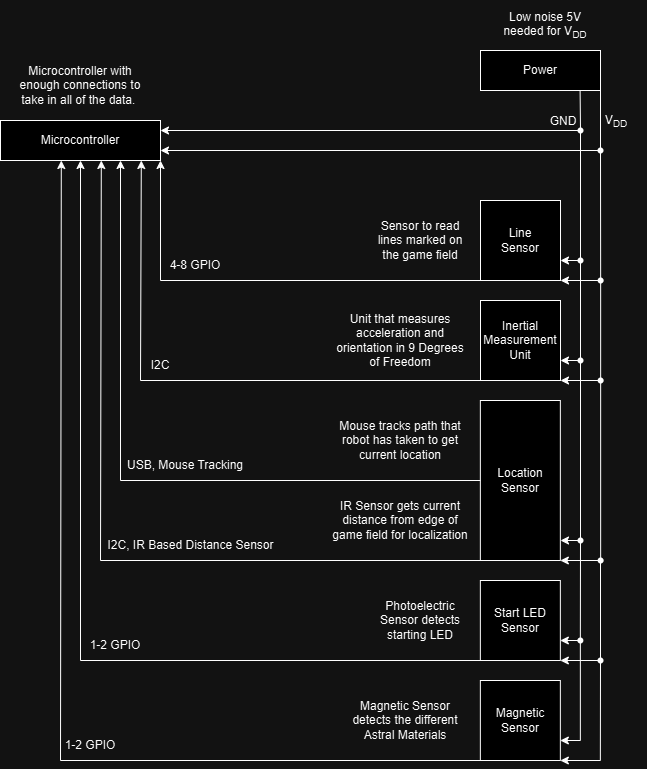
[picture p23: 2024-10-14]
Reports/Images and Sources/Conceptual Design/Sensor_Subsystem_V1.png

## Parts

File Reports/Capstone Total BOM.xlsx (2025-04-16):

Total: | $1025.72
Navigation Total: | $304.97
Navigation
Jetson Nano | Nvidia | 1 | $224.99 | $224.99 | https://www.amazon.com/onboard-Robotics-Machine-Learning-Version/dp/B0B8DMPWJL
SD Card (256 GB, UHS-1) | Western Digital, Inc. | 1 | $29.99 | $29.99 | https://www.amazon.com/SanDisk-256GB-Extreme-UHS-I-Memory/dp/B09X7CFXSX
SanDisk Professional PRO-Reader SD and microSD | Western Digital, Inc. | 1 | $49.99 | $49.99 | https://www.amazon.com/dp/B0B2X4FGYH
Motor Control Total: | $189.44
Motor Control
Arduino Mega | Arduino | 1 | $43.56 | $43.56 | https://www.amazon.com/ARDUINO-MEGA-2560-REV3-A000067/dp/B0046AMGW0?mcid=7091fc990cb33b948372fc448382ff81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
4 Pack L298N Motor Drive Controller Board DC Dual H-Bridge | AITRIP | 1 | $9.99 | $9.99 | https://www.amazon.com/Controller-H-Bridge-Stepper-Control-Mega2560/dp/B07WS89781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
Electronics Kit Compatible with Arduino | ELEGOO | 1 | $15.99 | $15.99 | https://www.amazon.com/ELEGOO-Electronics-Potentiometer-tie-Points-Breadboard/dp/B09YRJQRFF
Pololu Dual VNH5019 Motor Driver Shield for Arduino | Pololu | 2 | $59.95 | $119.90 | https://www.pololu.com/product/2507
Camera Total: | $309.67
Camera
Intel RealSense depth camera D435 | Intel | 1 | $309.67 | $309.67 | https://www.amazon.com/Intel-Realsense-D435-Webcam-FPS/dp/B07BLS5477?s=hi
Sensors Total: | $106.92
Sensors
Photoresistor | WODEYIJIA | 1 | $16.49 | $16.49 | https://www.amazon.com/Juried-Engineering-Photoresistor-GL12528-Sensitive/dp/B08F3WPNPF
Solderful Breadboard | DIGIKEY | 1 | $2.49 | $2.49 | https://www.digikey.com/en/products/detail/digikey/DKS-SOLDERBREAD-01/21274484
OTOS | Sparkfun | 1 | $79.95 | $79.95 | https://www.amazon.com/SparkFun-Optical-Tracking-Odometry-Sensor/dp/B0D6LQGBSK
Hall Effect Sensor 3Pins Magnetic Detector | ALLECIN | 1 | $7.99 | $7.99 | ALLECIN 20Pcs 49E OH49E SS49E S49E TO-92S Hall Effect Sensor 3Pins Magnetic Detector: Amazon.com: Industrial & Scientific (https://www.amazon.com/ALLECIN-Effect-Sensor-Magnetic-Detector/dp/B0CZ6RL4B2)
Power Total: | $114.72
Power
DC-DC Step Down Converter | DFRobot | 2 | $4.90 | $9.80 | https://www.digikey.com/en/products/detail/dfrobot/DFR0379/7087190?gclsrc=aw.ds&gad_source=1&gclsrc=aw.ds
Zeee 11.1V 80C 5200mAh 3S Lipo Battery (2 Pack) | Zeee | 1 | $70.99 | $70.99 | Amazon.com: Zeee 11.1V 80C 5200mAh 3S Lipo Battery with EC5 Connector Hardcase Battery for RC Car Boat Truck Helicopter Airplane Racing Models(2 Packs) : Toys & Games (https://www.amazon.com/Zeee-Connector-Hardcase-Helicopter-Airplane/dp/B08696WZMK?ref_=ast_sto_dp)
2 Male + 2 Female 12 V 2.1x5.5mm DC Power Jack Plug Adapter Barrel Connector | California JOS | 1 | $3.97 | $3.97 | Amazon.com: 2 Male + 2 Female 12 V 2.1x5.5mm DC Power Jack Plug Adapter Barrel Connector for CCTV Security Camera LED Strip : Electronics (https://www.amazon.com/California-JOS-Male-Female-2-1x5-5mm/dp/B0CR8TZ41W)
AUSTOR 560 Pieces Jumper Wire Kit 14 Lengths | AUSTOR | 1 | $9.99 | $9.99 | https://www.amazon.com/AUSTOR-Lengths-Assorted-Preformed-Breadboard/dp/B07CJYSL2T
1 in 3 Out DIY Mini Splice Compact Quick Electrical Connector | XALXMAW | 1 | $9.98 | $9.98 | XALXMAW 10Pcs Lever Wire Connectors, 1 in 3 Out DIY Mini Splice Compact Quick Electrical Connector, 24-12 AWG: Amazon.com: Industrial & Scientific (https://www.amazon.com/XALXMAW-Connectors-Splicing-Splitter-Electrical/dp/B0B28GPP5B)
3 Pairs EC5 5.0mm Male and Female Banana Connector Pigtails with 12awg 5.9inch | LinsyRC | 1 | $9.99 | $9.99 | Amazon.com: LinsyRC 3 Pairs EC5 5.0mm Male and Female Banana Connector Pigtails with 12awg 5.9inch Silicone Wire for RC Hobby Lipo Battery : Toys & Games (https://www.amazon.com/LINSYRC-Connector-Pigtails-5-9inch-Silicone/dp/B0BLLL4FFS?hvadid=80539416691913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)
Not on Final Robot but Ordered Total: | $839.83
Not on Final Robot but Ordered
Pololu Dual MC33926 Motor Driver Shield for Arduino (Item 2503) | Pololu | 1 | $34.99 | $34.99 | https://www.amazon.com/gp/product/B07LH5RPGJ/ref=ewc_pr_img_1?smid=A1283MCABFXB0Q&psc=1
Greartisan DC 12V 200RPM Turbo Worm Geared Motor | Greartisan | 1 | $14.99 | $14.99 | https://www.amazon.com/Greartisan-120RPM-Turbine-Reduction-JSX69-370/dp/B08K7HNXTM
High-Speed 0.6"/sec Linear Actuator 12v | Rtisgunpro | 1 | $18.99 | $18.99 | https://www.amazon.com/High-Speed-Actuator-actuators-Cabinets-Automation/dp/B09X994MGX
4Pcs Thin Film Pressure Sensor 20g-2Kg | MakerHawk | 1 | $11.99 | $11.99 | https://www.amazon.com/Pressure-Sensitivity-Sensitive-Industrial-Measurement/dp/B0CZ6L5NMM
30:1 Metal DC Geared-Down Motor 37Dx67.5L mm 6V/12V, with 64 CPR Encoder | CQRobot | 1 | $33.99 | $33.99 | https://www.amazon.com/dp/B08ZK9KVHF?ref=emc_s_m_5_i_atc&th=1
35kg high Torque Coreless Motor servo | ZOSKAY | 1 | $28.99 | $28.99 | https://www.amazon.com/ZOSKAY-Coreless-Digital-Stainless-arduino/dp/B07S9XZYN2?hvadid=693398985551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
LiDAR | Sparkfun | 3 | $81.25 | $243.75 | https://www.mouser.com/ProductDetail/SparkFun/SEN-18009?qs=iLbezkQI%252BsjpCIKpfdq6BA%3D%3D
Qwiic Connector Set | elechawk | 1 | $9.99 | $9.99 | https://www.amazon.com/elechawk-SparkFun-Development-Breadboard-Connector/dp/B08HQ1VSVL
4-port Qwiic I2C Bus | Sparkfun | 2 | $6.50 | $13.00 | https://www.amazon.com/SparkFun-MultiPort-connectors-Alternative-configuration/dp/B09M9BX55S
5pcs ACS712 20A Range Current Sensor Module Detector ACS712ELC 5A 20A 30A Amps Amperage (20A) | UMLIFE | 2 | $11.99 | $23.98 | https://www.amazon.com/UMLIFE-Current-Detector-ACS712ELC-Amperage/dp/B091YD9WP2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
OTOS | Sparkfun | 1 | $79.95 | $79.95 | https://www.amazon.com/SparkFun-Optical-Tracking-Odometry-Sensor/dp/B0D6LQGBSK
Green LED | LED TECH | 2 | $0.31 | $0.62 | https://www.newark.com/led-technology/l02r5000q1/led-green-t-1-3-4-5mm-3-7mcd-567nm/dp/97K4041
White LED Backlight Module - Medium 23mm x 75mm | Lucky Light | 1 | $6.75 | $6.75 | Amazon.com: White LED Backlight Module - Medium 23mm x 75mm : Tools & Home Improvement (https://www.amazon.com/White-LED-Backlight-Module-Medium/dp/B00R5CDHNI)
Hall Effect Sensor | Diodes INC | 3 | $0.48 | $1.44 | https://www.mouser.com/ProductDetail/Diodes-Incorporated/AH49FZ3-G1?qs=dZoB6MK9LKPUjOBJDQRw%2FA%3D%3D
ZEUS Battery Products Charger | ZEUS Battery Products | 1 | $131.04 | $131.04 | https://www.digikey.com/en/products/detail/zeus-battery-products/PCCG-LFP14-4V10A/9828828
Power Sonic Corporation Battery | Power Sonic Corporation | 2 | $80.20 | $160.40 | https://www.digikey.com/en/products/detail/power-sonic-corporation/PSL-SC-1270-F2/13577482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
3-Pack T Plug Male Connector to Female Connector Adapter Extension Cable | LinsyRC | 1 | $8.99 | $8.99 | Amazon.com: LinsyRC 3-Pack T Plug Male Connector to Female Connector Adapter Extension Cable with 11.8inch 14AWG Wire for RC Battery Toy DIY Spare Part : Toys & Games (https://www.amazon.com/dp/B0BDF8WLL6?s=industrial&sp_csd=d2lkZ2V0TmFtZT1zcF9kZXRhaWw)
12 V to 3.3 V / 5 V / 12 V DC-DC Voltage Converter Multi-Output Step-Down Power Supply | DGZZI | 2 | $7.99 | $15.98 | Amazon.com: DGZZI 2PCS 12 V to 3.3 V / 5 V / 12 V DC-DC Voltage Converter Multi-Output Step-Down Power Supply Module for Arduino : Electronics (https://www.amazon.com/DGZZI-Voltage-Converter-Multi-Output-Step-Down/dp/B07RKMZY8S)

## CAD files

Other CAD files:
Reports/Poster Template/Images/INN_Topology.dwg

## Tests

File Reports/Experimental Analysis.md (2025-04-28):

# Introduction

This experimental analysis revisits the conceptual design of our autonomous robot for the IEEE SECON 2025 hardware competition. The project's overarching goal was to design and build a robust and consistent robot capable of achieving a high score in the competition by reliably performing the core tasks of astral material collection, sorting, and placement within the allotted three minutes.

Based on the conceptual design and the outlined competition rules, the most critical requirements and success criteria directly impacting the project's have been split by subsystem for ease of testing.

# Motor Control

## Relevant Critical Success Criteria:
- Specification 1d: The drivetrain motors shall be able to operate under a load of up to 12 kg.

- Specification 1e:  The sorting and collecting motor systems for astral material shall be able to transfer and carry the load of at least one astral material at a time (3D printed icosahedrons, 48.2 g each for Geodinium).

- Specification 1f:  The Cosmic Shipping Container motors shall be able to carry and support most of the load from a full container of astral material 18 Geodinium for a total of 867.7 g.

- Specification 4:   The motors shall be capable of reversing the robot in the case that reversing the robot is the only method of not damaging the game field walls [S4].

The above critical success criteria prompt tests for the performance limits of all motors involved in this subsystem. Specifications 1e and 1f will be combined into one experiment that will test the performance of the sweeper, auger, sorting gate, and cosmic shipping container mechanism. The entire process of astral material collection and its process flow will be evaluated at its extremes in order to be prepared for what the team may face in a real run at the competition. Likewise, Specifications 1d and 4 will enable tests of the limits of the drivetrain for potential worst case scenarios at the competition. 

## Experiment One: Astral Material Collection

1.  **Purpose and Justification**:
    
This is an experiment that combines constraints 1e and 1f for the purpose of testing the full flow of astral material through the robot. Constraint 1e addresses the need for the robot mechanisms to be able to transfer at least one astral material at a time from the point of collection to the point of the cosmic shipping container. The sweeper motor, auger motor, and sorting servo are involved in this process as the astral material makes its way toward the shipping containers. Constraint 1f addresses the need for the servos and linear actuators involved in the shipping container arm mechanism to be able to hold and fully support a full load of the heaviest configuration of astral material, which is all 18 Geodinium pieces (slightly heavier than the non-magnetic Nebulite). Therefore, this experiment fulfills both requests by properly simulating the flow of material through the robot and testing the support capabilities of the shipping container mechanism. Criteria of success will include the number of pieces that make it to the container and whether the container (after being picked up off the ground) stayed suspended or not. Also, completing a few trials with different material transfer sequences will help provide an overall picture of how the robot would perform given the unpredictable material placement. 

2.  **Detailed Procedure**:
    
The test involves keeping the robot stationary but providing power to the following motors/servos for material flow: the sweeper motor, the auger motor, the sorting servo, the linear actuator, and the shipping container arm servo. Run the function for grabbing the container via the serial input on the Arduino code until compression by the actuator is successful. Then, turn on the sweeper and auger, and move Geodinium material into the sweeper, one by one, in 10 second intervals. Continue this process until all 18 Geodinum have reached the container and then lift the robot off the ground to see if it can completely support the container when suspended.

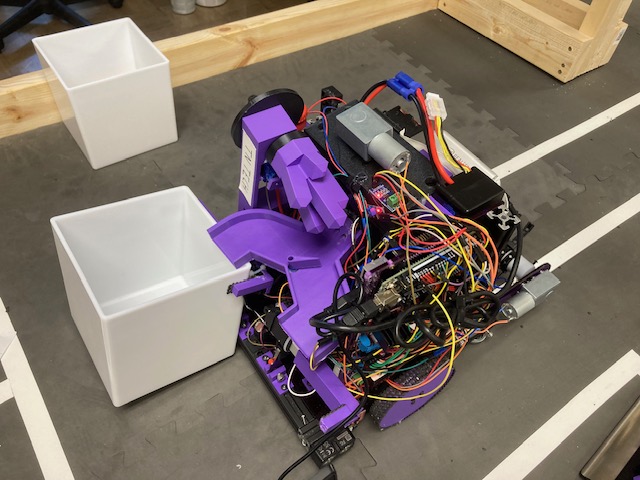
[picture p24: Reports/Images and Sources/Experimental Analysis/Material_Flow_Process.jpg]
Material Flow Process


3.  **Expected Results**:
    
I would expect the robot to be fully capable of transferring the material and supporting the full load due to results from prior testing. However, there may be some slip on the hold of the shipping container, which would not be ideal as the container will already be positioned close to the ground. A complete success would be no slip, but I expect to at least see some movement.

4.  **Actual Results**:
    
The following were weights that were considered to determine the full maximum load of Geodinium:

Cosmic shipping container: 0.364 kg 

Robot Weight +  shipping container: 4.150 kg

Robot Weight: 3.786 kg

1 Nebulite: 0.010 kg

16 Total Nebulite: 0.16 kg

1 Geodinium: 0.040 kg 

18 Total Geodinium: 0.72 kg

18 Geodinium pieces were not available, so the total weight of 18 Geodinium (0.72 kg) was simulated by using the available 15 Geodinium plus 13 Nebulite. The same intended material flow process was still used, just for 28 total pieces instead of 18. 

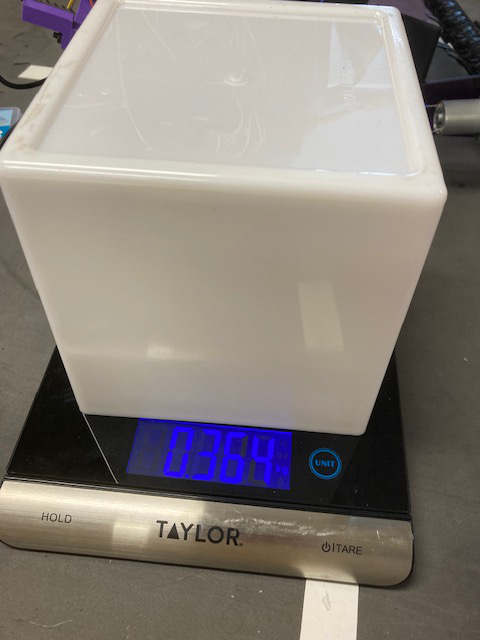
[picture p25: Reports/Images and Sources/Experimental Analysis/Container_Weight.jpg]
Container Weight


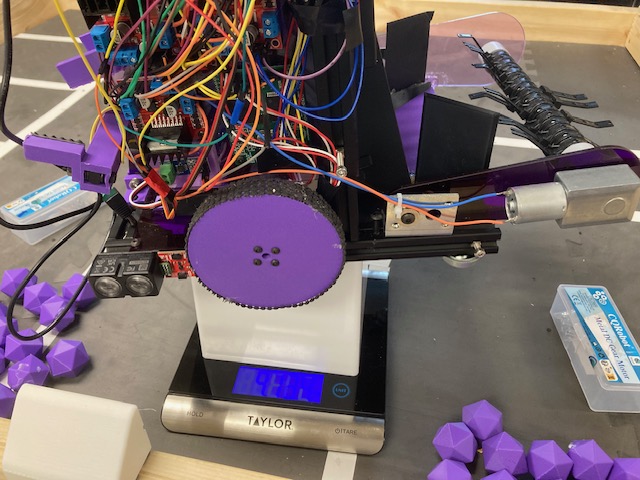
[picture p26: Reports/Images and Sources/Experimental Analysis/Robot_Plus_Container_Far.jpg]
Robot Plus Container Far


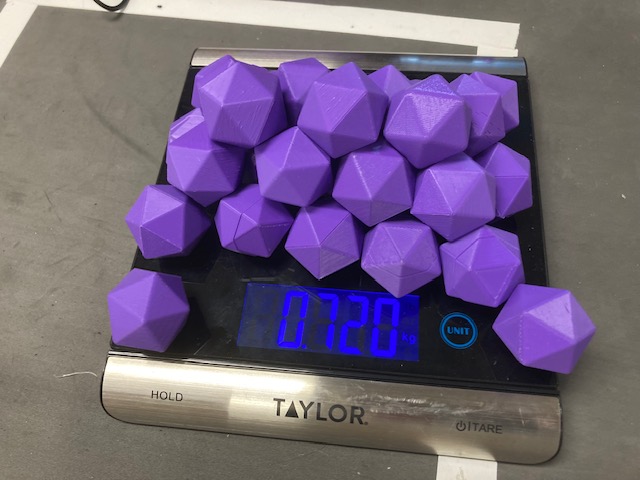
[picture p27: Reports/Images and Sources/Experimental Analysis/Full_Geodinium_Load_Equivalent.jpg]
Full Geodinium Load Equivalent


| Trial | Order of Material Entry | Number of Material Successfully Transferred (out of 28) | Did Cosmic Shipping Container Remain Supported? |
| :-- | :--- | :--- | :--- |
| 1 | Nebulite, then Geodinium, then Geodinium glue pieces | 26 | Yes - lift robot test worked |
| 2 | Alternating until Geodinium only, then glue pieces | 24 | Yes - lift robot test worked |
| 3 | Geodinium, then Nebulite, then glue pieces | 12 | Yes - lift robot test worked |
| 4 | Geodinium, then Nebulite, then glue pieces | 26 | Yes - lift robot test worked |

5.  **Interpretation and Conclusions**:
    
- Provide a detailed analysis explaining the significance of the results.

Trial 1 successfully transferred 26 out of the 28 attempted pieces, and when the lift test was attempted, the robot successfully maintained grip on the cosmic shipping container. This means that the robot has the capability to support the weight of nearly a full load of Geodinium pieces, which is the maximum weight configuration. The two that did not make it were stuck on the sorting station chute. These pieces were the last to go through the robot, which may mean the backend of material flow will be less successful.

Trial 2 was still mostly successful with 24 out of 28 transferred. The last 4 that were left to transfer ended up getting stuck on the sorting station platform. This group was composed of two Nebulite and the same two pieces that got stuck on Trial 1, which have an excess of glue on them. The robot did successfully maintain a grip on the cosmic shipping container. This trial continues to support the theory that the last pieces that go through the sorting station will not make it to the shipping container. 

Trial 3 was not successful in material flow, but it did maintain grip on the shipping container. The material pieces were almost halfway through being transferred when an accumulation of material began to build up on the sorting station. Like Trial 2, this build up consisted of 4 pieces. Unlike Trial 2, all 4 were standard Nebulite pieces, and the build up was backed up toward the station entrance rather than being more spread out, which occurred in Trial 2. The build up was followed by another piece that got near the top but couldn’t get to the entrance and caused the auger motor to stall. It seems that the light weight of the Nebulite may have helped cause this buildup, as all four pieces involved were Nebulite. 

A fourth trial was tested in order to provide a larger sample size for the sequence of material that caused the most error. In the same configuration of all Geodinium, followed by all Nebulite, and finally the two remaining glue pieces, every piece was transferred except for the glue pieces. These two were then manually inserted into the container just to confirm the lift test for the full load, and the load was still successfully lifted. 

- State whether results matched your expectations and explain any discrepancies.

These results mostly match my expectations, as most of the material was transferred smoothly and there was very little slip on the container hold. However, the two pieces that did not make it in Trial 1 need to be addressed. These pieces had a significant amount of glue on their exterior, which likely made transport more difficult through the increased friction. These pieces were also the last two. One observation for all trials that I had was that most of the time, material would get stuck on the servo chute platform, but would be pushed into the container by the next one after it. Therefore, if there is a need to push the material stuck on the chute, then it may be unlikely for the robot to transfer every material piece to the respective container. Just all of the ones that lead up to the last couple would be the most reliable. Also, if there is a long sequence of lighter pieces, then a buildup failure will be more likely to occur due to less weight forcing the pieces down the chute.

## Experiment Two: Drivetrain Performance

1.  **Purpose and Justification**:
    
Specification 1d covers the need for the drivetrain motors to be able to operate under the maximum possible load. However, the robot should never realistically reach a load of 12 kg, so the load of the robot plus the full approximate load of astral material would be a more critical test. If the drivetrain motors can still enable translational and rotational movements for the robot with this load, all loads less than this will be feasible. Specification 4 states that the robot should be capable of effectively reversing at field walls without inflicting damage to them. This movement can be tested under the full load of Specification 1d. Also, this test will not involve the use of navigational correction capabilities, as it is meant to test the pure performance of the motors alone. Therefore, some error accumulation for the paths tested is to be expected, but the main aspect of the motors that will be evaluated is the translational and rotational speed under a heavy load.

2.  **Detailed Procedure**:
    
First, use all of the available astral material from the previous experiment (15 Geodinium plus 13 Nebulite) and the extra remaining to simulate a nearly full configuration of all astral material. The original amount of 15 Geodinium and 13 Nebulite can be put into the Geodinum-side shipping container and pulled up by the robot. The remaining can be dispersed throughout the material flow system. In order to escape from the corner of the field as requested by Specification 4, put the robot at either of the two telemetry corners aligned with the longer side wall, as seen in the picture below. Then test the rotational capabilities of the robot by backing out into the center of the field by giving a serial input negative speed for each motor. The right motor should be double that of the left motor when starting from the configuration seen in the picture. This would be flipped if the position was also flipped to the other corner. Complete several trials with varying motor speeds between 0-100 to determine the general performance of the robot under the heavy load. Success will be determined by whether the robot reverses out of the corner without being impeded by the walls and whether the robot successfully maintains the container grip. 

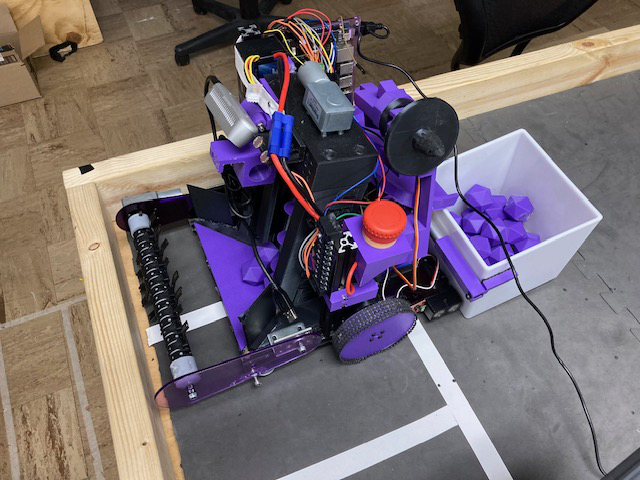
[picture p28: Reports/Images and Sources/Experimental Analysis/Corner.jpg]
Corner


Another test that will be done involves the purely translational capabilities of the robot, seeing how straight of a line the robot can make when it is not subject to error-correcting navigation, also with varied speeds. Starting at the front of the white line spanning the telemetry zones facing the cave, center the robot with the intention of allowing a straight path from the white line to the cave. Success will be determined by whether the robot makes it to the cave entrance and whether the robot maintains the container grip. 

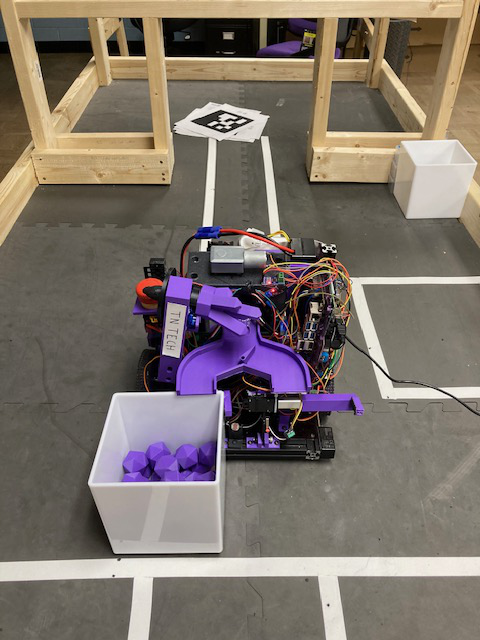
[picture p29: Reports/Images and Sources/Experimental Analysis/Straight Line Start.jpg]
Start


3.  **Expected Results**:
    
I would expect the robot to be mostly capable of completing this task with the heavy load, but it may have issues at lower speeds. Also, I expect the robot to veer to the left some in the straight line test due to the Geodinium shipping container and the lack of error correction. However, at full speed the robot should be more than capable of any movement across the board with the full load, even if it isn’t completely accurate. 

4.  **Actual Results**:

### Escape Corner Test

| Trial | Left Speed | Right Speed | Escaped Corner? | Maintained Container Grip? |
| :-- | :--- | :--- | :--- | :--- |
| 1 | -50 | -100 | Yes | Yes |
| 2 | -25 | -50 | Yes | Yes |
| 3 | -12.5 | -25 | No - remained stationary | Yes |

### Straight Line Test

| Trial | Left Speed | Right Speed | Made it to the cave? | Maintained Container Grip? |
| :-- | :--- | :--- | :--- | :--- |
| 1 | 100 | 100 | No - veered left | Yes |
| 2 | 50 | 50 | No - veered more left than Trial 1 | Yes |
| 3 | 25 | 25 | No - remained stationary | Yes |

5.  **Interpretation and Conclusions**:
    
- Provide a detailed analysis explaining the significance of the results.

For the Corner and Straight Line Tests, the speed for each motor was gradually decreased per each of the three trials. Regarding shared results, the grip of the container was maintained for all trials of each test. 
For the Corner Test, the maximum speed of 100 on the given range was used for the right motor, with the left motor being half of that on Trial 1. The resulting performance had the robot quickly and easily reverse out of the corner into the open field, as seen in the picture below.

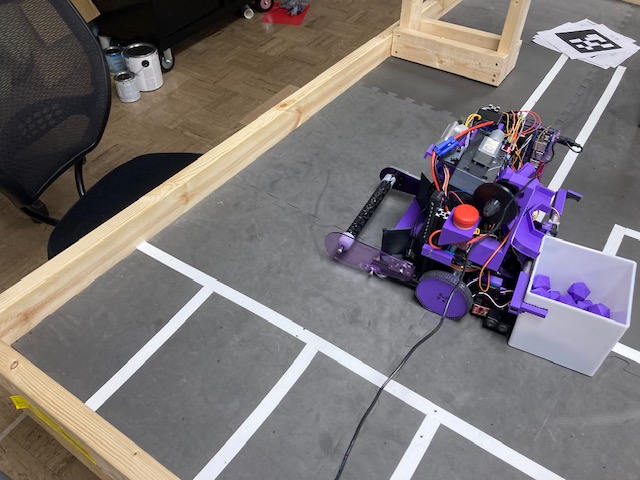
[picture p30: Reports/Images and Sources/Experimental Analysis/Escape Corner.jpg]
Escape Corner


The same general behavior occurred again for the second trial with the left and right motor speeds being half of Trial 1. However, when this was halved again for Trial 3, the robot would not budge, signifying that this final left and right motor speed pairing was not enough to allow movement with the full load. 

For the Straight Line Test, the maximum speed of 100 was used for both motors on Trial 1, and the result was that the robot easily traversed the field to the side of the cave, but it did not make it to the cave as the robot veered to the left along the path. For Trial 2 with halved speeds for both motors, the same result occurred, this time with more error and a slower time of completion. For Trial 3 with the motor speeds halved again, the robot did not budge from the start line. 

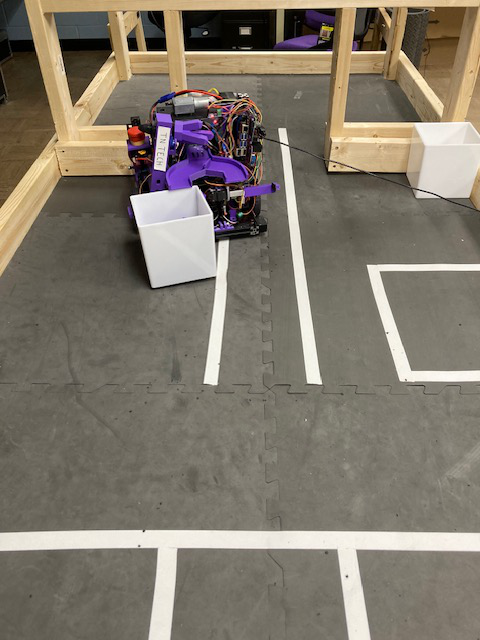
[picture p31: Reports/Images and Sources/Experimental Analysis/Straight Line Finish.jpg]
Finish


Regarding the significance of the results in both tests, it seems the full speed is more than enough to complete translational and rotational movement quickly across the field. However, motor speeds nearing the 25 range were not enough to allow either type of movement between both tests. The robot did successfully remove itself from the corner each time it had enough speed, so the robot is capable of satisfying Specification 4. The robot also did all of these movements for each test with the described full load, which would meet the realistic expectations for Specification 1d. The only issue present for the drivetrain was the lack of accuracy in the robot path, which emphasizes the necessity of a feedback system for error correction using the navigation subsystem. 

- State whether results matched your expectations and explain any discrepancies.

These results for each test matched my expectations. I expected the robot to be able to move with the maximum speed, but I wasn’t aware of how quickly it would move. The robot exceeded my expectations with regard to its quick response movement at full speed. I did expect the drop off in performance as the speed decreased to quarter speed. I did not expect the robot to veer to the left excessively as demonstrated in the Straight Line Test, but I did expect some error. The shipping container touching the ground may have been the source of issue for drastic leftward error. 

## Summary of All Experiments

As demonstrated by the Astral Material Collection Experiment and the Drivetrain Performance Experiment, all motors involved in movement and material flow, including the sweeper motor, auger motor, sorting gate servo, drivetrain motors, linear actuator, and shipping container servo function as intended and when prompted. There were some physical issues involved in testing that prohibited further success for material transfer and drivetrain movement, but each of the motors were proven to meet the realistic expectations of the given specifications and were thus proven to be prepared to test the limits of any potential competition run. 

# Sensors

## Critical Aspects of Sensors

Specifications:
1.	The robot's distance measurement sensor shall be able to find the walls of the game field and the cave.
2.	The robot's light detector shall be able to detect when the start LED turns on.
3.	The robot's magnetic sensors shall be able to detect the magnetic fields of the Geodinium.
4.	All of the robot's sensors shall be able to work effectively despite background interference in the competition environment.

Constraints:
1.	The robot shall know its current position.
2.	The magnetic sensor shall provide a signal that is larger than the resolution of the Arduino's Analog-to-Digital Converter.
3.	The light detector shall provide a signal visible through the background noise.

The sensor subsystem needs to know the robot’s location to avoid walls and stay on the game field. The subsystem helps gain points by sorting materials and using the referee controlled starting LED. These sensors need to work in a noisy environment and provide readable signals.

## Sensors Experimental Overview
The sensors subsystem has 3 main components. There is the Optical Tracking and Odometry Sensor (OTOS), photoresistors, and hall effects. Each of these components will be tested on the robot to verify that it works properly with the total system.

## Purpose and Justification:
### OTOS
The accuracy of the linear and angular displacements was measured. By knowing the accuracy of the OTOS, the navigation can set narrower tolerances on the area of the destination point. This will allow the robot to travel to more precise locations. If the robot does not know its current location well enough, it will fail. A different method available is to use distance sensors.

### Hall Effect
The range and noise of the hall effect sensors were measured. This determines the tolerance for detecting magnetic material. If the noise is too large and the signal is too small, the signal will be lost. If the robot cannot detect magnetic materials, it will not sort them. This is alright as the robot will still score points for putting materials in the wrong bin.

### Photoresistor
The number of accurate start LED detections was counted. This would determine if there were any false readings and how often they would happen. This experiment would find if the robot would ever have a false start or not start. If the robot does not start successfully, a different start method would need to be built. A long timer was used before, but a button or switch would be the best.

## Detailed Procedure:
### OTOS
The OTOS was left attached to the robot. If there was any issue with how level the OTOS was, it would be discovered and fixed. Since the OTOS was tested on the robot, the drive wheels were removed to reduce noise from the forced spin of the motors. Data is taken with the Jetson Nano. The starting point is always set as (0, 0, 0) for X, Y, and heading.  The ending point is the same. Only the final position point is recorded.
For the linear displacement experiment, the robot was rolled on neutral wheels on a flat surface against a flat object. The robot was moved forward 105 inches by hand, back to the start and repeated 3 times in a single run for a total of 630 inches. The robot had the same starting and ending position to easily compare the drift. The choice of total distance was arbitrary but was suggested by the manufacturer to be more than 100 inches to see significant drift. The larger the distance, the easier it was to see the drift and measure its offset. The robot was not rotated when the linear displacement was tested.

For the angular displacement experiment, the robot was spun on neutral wheels on a flat surface. It would start against a flat object and then was positioned back on the same flat object, so it had the same starting and ending angle. The robot was spun counterclockwise ten times by hand in a single run for a total of 3600 degrees. The choice of total angular rotation was suggested by the manufacturer to be at least 3600 degrees to see significant drift. The larger the distance, the easier it was to see the drift and measure its offset.

The image below shows the OTOS attached to the bottom of the robot.

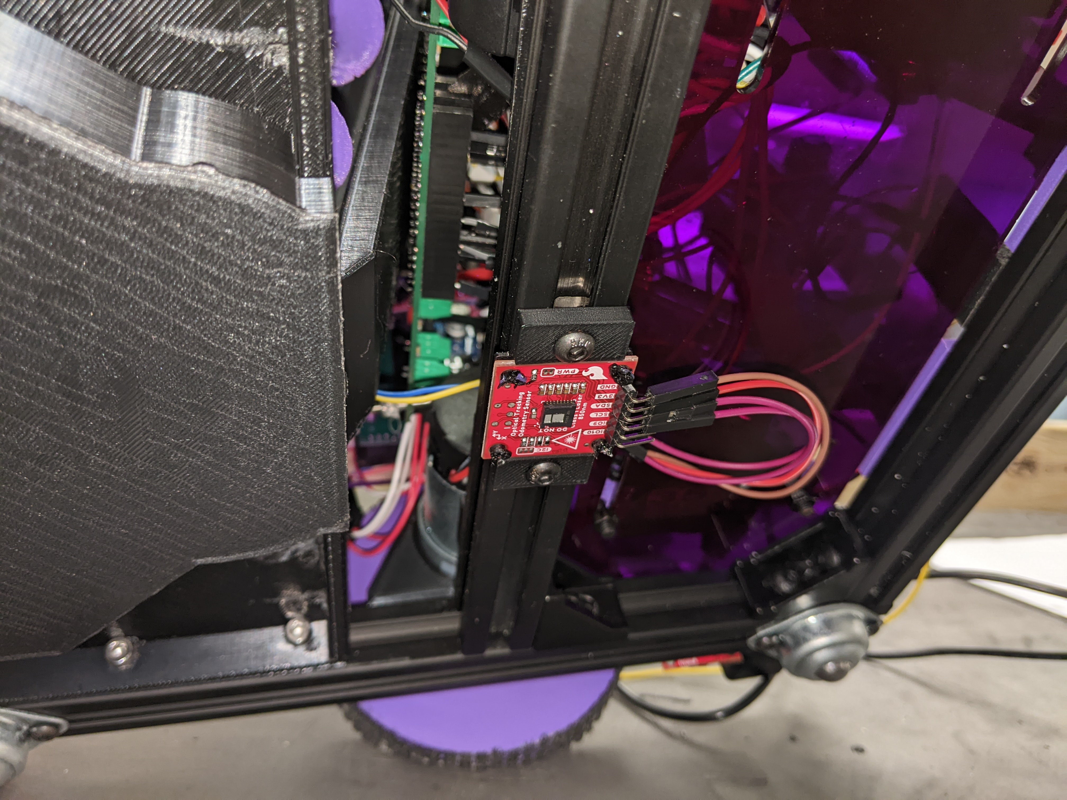
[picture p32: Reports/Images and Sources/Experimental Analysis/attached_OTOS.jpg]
Attached_OTOS

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

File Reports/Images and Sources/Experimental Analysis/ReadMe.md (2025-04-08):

This folder holds photos used in the Experimental Analysis.

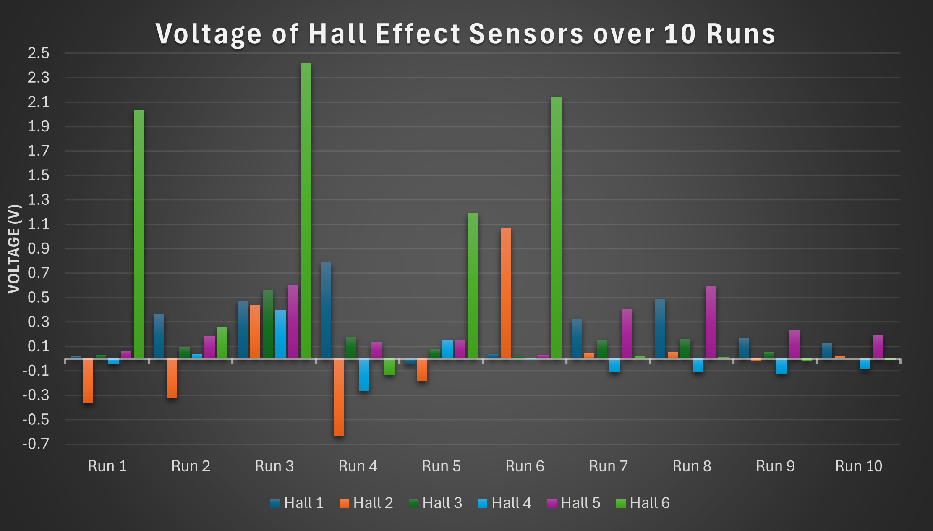
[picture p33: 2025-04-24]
Reports/Images and Sources/Experimental Analysis/Full_Table_Hall_Effects.png

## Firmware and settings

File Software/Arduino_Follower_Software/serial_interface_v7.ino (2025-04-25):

#include <TimerOne.h>
#include "const_declarations.h"
#include "nano_to_arduino.h"
#include "arduino_to_nano.h"
#include "sorter.h"

unsigned long t;
unsigned long t_prev = 0;
unsigned long matchTime;
float length = 0;
bool expand = false;
bool extend = false;
bool retract = true;
bool serial = true;
bool translated = false;
bool rotated = false;
bool pressureDetected;
bool int_state = false;
unsigned long previousMillis;

// ********************* Start of Package System *********************
// Define a struct to hold input data received from the Nano
struct InputData {
  //
  float leftWheelSpeed; // -100..100
  float rightWheelSpeed; // -100..100
  int auger; // -1: negative direction, 0: no rotation, 1: positive direction
  int sweeper; // -1: negative direction, 0: no rotation, 1: positive direction
  int beaconArm; // -1: negative direction, 0: no rotation, 1: positive direction
  int beaconGripper; // -1: negative direction, 0: no rotation, 1: positive direction
  int gscGripper; // -1: negative direction, 0: no rotation, 1: positive direction
  int nscGripper; // -1: negative direction, 0: no rotation, 1: positive direction
  int gscLeaner; // -1: negative direction, 0: no rotation, 1: positive direction
  int nscLeaner; // -1: negative direction, 0: no rotation, 1: positive direction
};


// Example command received: 0,0,1,0,0,0,0,0,0,0

// Define a struct to hold output data to be sent to the Nano
struct OutputData {
  int sweeperCurrentSensor; // 0: not stalled, 1: stalled
  int augerCurrentSensor; // 0: not stalled, 1: stalled
  float gscPressureSensor; // 0..100 (full pressure)
  float nscPressureSensor; // 0..100 (full pressure)
  int gscLimitSwitch; // 0: not pressed, 1: pressed
  int nscLimitSwitch; // 0: not pressed, 1: pressed
  int photosensor; // 0: not detected, 1: detected
};

// Global variables for serial data reception
String inputString = "";
bool newData = false;

// Timer variables for sending output data every 100 ms
unsigned long lastSendTime = 0;
const unsigned long sendInterval = 100;  // in milliseconds



// Function declarations
void readSerialData();
InputData parseInputData(const String &packet);
String buildOutputPacket(const OutputData &data);

void setup() {
  Serial.begin(115200);
  pinMode(gscLimitSwitchPin, INPUT);
  pinMode(nscLimitSwitchPin, INPUT);
  pinMode(ambientPhotoSensorPin1, INPUT);
  pinMode(ambientPhotoSensorPin2, INPUT);
  pinMode(detectingPhotoSensorPin, INPUT);
  pinMode(hallEffectPinX, INPUT);
  pinMode(hallEffectPinY, INPUT);
  pinMode(hallEffectPinZ, INPUT);
  

  // Set Actuator motor driver pins
  pinMode(gscGripperPWMPin, OUTPUT);
  pinMode(gscGripperDirPin1, OUTPUT);
  pinMode(gscGripperDirPin2, OUTPUT);
  pinMode(nscGripperPWMPin, OUTPUT);
  pinMode(nscGripperDirPin1, OUTPUT);
  pinMode(nscGripperDirPin2, OUTPUT);

  // Set sweeper and sweeper arm driver pins
  pinMode(sweeperPWMPin, OUTPUT);
  pinMode(sweeperDirPin1, OUTPUT);
  pinMode(sweeperDirPin2, OUTPUT);

  // Set Auger driver pins
  pinMode(augerPWMPin, OUTPUT);
  pinMode(augerDirPin1, OUTPUT);
  pinMode(augerDirPin2, OUTPUT);

  // Set Servo system pins
  gscLeanerServo.attach(GSCServoPin);
  nscLeanerServo.attach(NSCServoPin);
  pinMode(augerCurrentPin, INPUT);
  pinMode(sweeperCurrentPin, INPUT);
  limG.setDebounceTime(1); // set debounce time to 1 millisecond
  limN.setDebounceTime(1); // set debounce time to 1 millisecond
  limS.setDebounceTime(1); // set debounce time to 1 millisecond

  SortServo.attach(SortServoPin);
  SortServo.write(135); // 90 +-45
  gscLeanerServo.write(107);
  nscLeanerServo.write(desiredAngleNSC);

  pinMode(beamBreak, INPUT);













// CHECK THAT THESE ARE THE CORRECT SERVOS ********************************************************************



  // before
  /*
  BaseServo.attach(beaconBasePin);
  WristServo.attach(beaconWristPin);
  BaseServo.write(initialAngleBase);
  WristServo.write(initialAngleWrist); 
  */
  // after
  beaconGripperServo.attach(beaconGripperPin);
  beaconArmServo.attach(beaconArmPin);
  beaconGripperServo.write(initialAngleBeaconGripper);
  beaconArmServo.write(initialAngleBeaconArm); 

  matchTime = millis();  // Start tracking match time


  //Serial.println("Arduino integrated send & receive ready...");
}







// FINISH SORT, HALL EFFECT, AND OBJECT DETECTION







void loop() {
limG.loop(); // MUST call the loop() function first
limN.loop(); // MUST call the loop() function first

  // Continuously check for incoming data
  readSerialData();
  
  // When a complete input packet is received (terminated by '\n')
  if (newData) {
    
    lastSendTime = millis();
    InputData inputData = parseInputData(inputString);
    
    // Debug print for input data
    //Serial.println("Debug | Received input data at " + millis());
    /*Serial.print("debug -  Left wheel speed: ");
    Serial.println(inputData.leftWheelSpeed);
    Serial.print("debug -  Right wheel speed: ");
    Serial.println(inputData.rightWheelSpeed);
    Serial.print("debug -  Auger: ");
    Serial.println(inputData.auger);
    Serial.print("debug - Sweeper: ");
    Serial.println(inputData.sweeper);
    Serial.print("debug - Beacon Arm: ");
    Serial.println(inputData.beaconArm);
    Serial.print("debug - Beacon Gripper: ");
    Serial.println(inputData.beaconGripper);
    Serial.print("debug - GSC Gripper: ");
    Serial.println(inputData.gscGripper);
    Serial.print("debug - NSC Gripper: ");
    Serial.println(inputData.nscGripper);
    Serial.print("debug -  GSC Leaner: ");
    Serial.println(inputData.gscLeaner);
    Serial.print("debug - NSC Leaner: ");
    Serial.println(inputData.nscLeaner);
    Serial.println("-------------------------------------");*/

    // call all nano_to_arduino functions
    robotSpeedFunction(inputData.leftWheelSpeed, inputData.rightWheelSpeed);
    augerFunction(inputData.auger);
    sweeperFunction(inputData.sweeper);
    beaconArmFunction(inputData.beaconArm);
    beaconGripperFunction(inputData.beaconGripper);
    gscGripperFunction(0);
    nscGripperFunction(inputData.nscGripper);
    gscLeanerFunction(0);
    nscLeanerFunction(inputData.nscLeaner);
    
    // Reset for next input packet
    inputString = "";
    newData = false;


    
    
    // Simulate output data values; replace with your actual sensor readings
    OutputData outputData;
    //OutputData outputData;      // this was here twice for some reason. Should just be deleted but left it in case
    /*
    outputData.sweeperCurrentSensor = analogRea/*d(sweeperCurrentPin) > 500 ? 1 : 0;
    outputData.augerCurrentSensor = analogRead(augerCurrentPin) > 500 ? 1 : 0;
    outputData.gscPressureSensor = (analogRead(gscPressurePin) / 1023.0) * 100;
    outputData.nscPressureSensor = (analogRead(nscPressurePin) / 1023.0) * 100;
    outputData.gscLimitSwitch = digitalRead(gscLimitSwitchPin);
    outputData.nscLimitSwitch = digitalRead(nscLimitSwitchPin);
    outputData.photosensor = digitalRead(photoSensorPin);
    */

    // call all arduino_to_nano functions
    outputData.sweeperCurrentSensor = sweeperCurrentSensorFunction();
    outputData.augerCurrentSensor = augerCurrentSensorFunction();
    outputData.gscPressureSensor = gscPressureSensorFunction();
    outputData.nscPressureSensor = nscPressureSensorFunction();
    outputData.gscLimitSwitch = gscLimitSwitchFunction();
    outputData.nscLimitSwitch = nscLimitSwitchFunction();
    outputData.photosensor = photosensorFunction();
    

    // Build and send the output packet
    String packetToSend = buildOutputPacket(outputData);
    //Serial.println("Debug | Sent output data at " + String(millis()));
    Serial.println(packetToSend);
    //Serial.println(millis()-lastSendTime);
  }
  
  // Check if it's time to send output data (every 100 ms)
  //if (millis() - lastSendTime >= sendInterval) {
  //}
  sorter();
}











// Function definitions

// Reads available characters from Serial and flags when a newline is detected
void readSerialData() {
  while (Serial.available() > 0) {
    char c = (char)Serial.read();
    //Serial.write(c);
    if (c == '\n') {
      newData = true;
    } else {
      inputString += c;
    }
  }
}

// Parses a comma-separated string into an InputData struct
InputData parseInputData(const String &packet) {
  InputData data;
  int startIndex = 0;
  int commaIndex;
  
  // Helper lambda to extract the next field
  auto getNextField = [&]() -> String {
    commaIndex = packet.indexOf(',', startIndex);
    if (commaIndex == -1) {
      commaIndex = packet.length();
    }
    String field = packet.substring(startIndex, commaIndex);
    startIndex = commaIndex + 1;
    return field;
  };

  data.leftWheelSpeed  = getNextField().toFloat();
  data.rightWheelSpeed = getNextField().toFloat();
  data.auger           = getNextField().toInt();
  data.sweeper         = getNextField().toInt();
  data.beaconArm       = getNextField().toInt();
  data.beaconGripper   = getNextField().toInt();
  data.gscGripper      = getNextField().toInt();
  data.nscGripper      = getNextField().toInt();
  data.gscLeaner       = getNextField().toInt();
  data.nscLeaner       = getNextField().toInt();
  
  return data;
}

// Builds a comma-separated output packet from OutputData struct values
String buildOutputPacket(const OutputData &data) {
  String packet = "";
  packet += String(data.sweeperCurrentSensor)     + ",";
  packet += String(data.augerCurrentSensor)       + ",";
  packet += String(data.gscPressureSensor, 2)     + ",";
  packet += String(data.nscPressureSensor, 2)     + ",";
  packet += String(data.gscLimitSwitch)           + ",";
  packet += String(data.nscLimitSwitch)           + ",";
  packet += String(data.photosensor);
  return packet;
}

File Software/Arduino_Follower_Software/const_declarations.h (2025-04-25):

#ifndef CONST_DECLARATIONS_H
#define CONST_DECLARATIONS_H

#include <Arduino.h>
#include <Servo.h>
#include <ezButton.h>
// Global variable declarations for any and all constant values

extern Servo gscLeanerServo, nscLeanerServo, SortServo, beaconArmServo, beaconGripperServo;

extern ezButton limG, limN, limS;

extern float voltageAugerSensor, currentAugerSensor, voltageSweeperSensor, currentSweeperSensor;
extern float movingAverageAmbient1, movingAverageAmbient2, movingAverageDetecting,
      ambientSensorVoltage1, ambientSensorVoltage2, startLEDSensorVoltage;

// Define sensor pins - DOUBLE CHECK - checked
const int sweeperCurrentPin = A0;
const int augerCurrentPin = A1;
const int gscPressurePin = A2;
const int nscPressurePin = A3;
const int gscLimitSwitchPin = 2;
const int nscLimitSwitchPin = 3;
const int ambientPhotoSensorPin1 = A11;
const int ambientPhotoSensorPin2 = A12;
const int detectingPhotoSensorPin = A7;
const int hallEffectPinX = A13;
const int hallEffectPinY = A14;
const int hallEffectPinZ = A15;
const int beamBreak = 47;

const long interval = 8000;
const long intervalSG = 2000;

// A1 to auger
// A0 to roller
// 47 for beambreak
// Photoresistors: A7, A11, A12
// Start Photoresistor: A7
// Ambient Photoresistors: A11, A12
// Hall Effect Sensors: A13, A14, A15

/*
// Define pins for pressure sensors and current sensor
const int presG = A2;
const int presN = A3;

const int currentSGPin = A1; // Sensor signal wire. This is the auger sensor.
const int currentSNPin = A0; // Sensor signal wire. This is the sweeper sensor.
*/

const float sensorOffset = 2.57; // Zero current output (2.5V for ACS712)
const float sensitivity = 0.185;  // 100mV per A for 20A ACS712

const int presThreshold = 100;  // not currently used as the nano is processing theshold

// Motor Pins
const int leftDriveENPin = 26;
const int leftDriveDir1Pin = 10;
const int leftDriveDir2Pin = 11;
const int leftDrivePWMPin = 9;
const int leftDriveEncAPin = 20;
const int leftDriveEncBPin = 21;

const int rightDriveENPin = 27;
const int rightDriveDir1Pin = 12;
const int rightDriveDir2Pin = 13;
const int rightDrivePWMPin = 3;
const int rightDriveEncAPin = 18;
const int rightDriveEncBPin = 19;

// CSC Servo pins 
const int GSCServoPin = 44;
const int NSCServoPin = 40; 
const int SortServoPin = 45;

// I don't think these are needed
//const int sensorPin = A0; // Photoresistor
//const int threshold = 500; // division for magnetic representation

// Beacon Servo pins
const int beaconArmPin = 33;
const int beaconGripperPin = 43;
const int initialAngleGSC = 135; //125
const int desiredAngleGSC = 110;
const int initialAngleNSC = 135; //140  // this is actually pickup angle.
const int desiredAngleNSC = 155;    // this is actually initial angle. // go back here after pick up
const int initialAngleSortServo = 0;          // THIS VALUE ISN'T CORRECT****************************************
const int desiredAngleSortServo = 0;          // THIS VALUE ISN'T CORRECT****************************************
const int initialAngleBeaconArm = 0; //105
const int desiredAngleBeaconArm = 55; //170
const int initialAngleBeaconGripper = 90;
const int desiredAngleBeaconGripper = 35;  







// Actuator motor driver pins
const byte gscGripperPWMPin = 4, gscGripperDirPin1 = 36, gscGripperDirPin2 = 37; // PUT IN PIN 4 (PWM) - left/GSC motor
const byte nscGripperPWMPin = 5, nscGripperDirPin1 = 23, nscGripperDirPin2 = 22; // PUT IN PIN 5 (PWM) - right/NSC motor

// Auger driver pins
const byte augerPWMPin = 6, augerDirPin1 = 34, augerDirPin2 = 30;

// Sweeper, Sweeper Arm driver pins
const byte sweeperPWMPin = 7, sweeperDirPin1 = 53, sweeperDirPin2 = 52;
//const byte sweepArmPWMPin = 8, sweepArmDirPin1 = 48, sweepArmDirPin2 = 49;

/*

******* L298N Pin Locations for Above Arduino Pins *******

// Actuator motor driver pins
const byte actM1PWMPin = 4 to top_left_ENA, actM1DirPin1 = 36 to top_left_IN1, actM1DirPin2 = 37 to top_left_IN2; // left/GSC motor
const byte actM2PWMPin = 5 to bottom_ENB, actM2DirPin1 = 23 to bottom_IN3, actM2DirPin2 = 22 to bottom_IN4; // right/NSC motor

// Auger driver pins
const byte augerPWMPin = 6 to top_left_ENB, augerDirPin1 = 34 to top_left_IN3, augerDirPin2 = 30 to top_left_IN4;

// Sweeper, Sweeper Arm driver pins
const byte sweepPWMPin = 7 to bottom_ENA, sweepDirPin1 = 53 to bottom_IN1, sweepDirPin2 = 52 to bottom_IN2;
const byte sweepArmPWMPin = 8 to top_right_ENB, sweepArmDirPin1 = 48 top_right_IN3, sweepArmDirPin2 = 49 top_right_IN4;

*/


#endif

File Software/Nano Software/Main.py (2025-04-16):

import math
import asyncio
import logging
import sys
import csv
import qwiic_otos
import time
from datetime import datetime
from pathlib import Path
from ArduinoComms import ArduinoCommunicator
from EventHandler import EventHandler
from StateMachine import StateMachine
from Event import Event, EventType
from State import Vector2, Vector3, Transform
from MotorControl import InputPacket, OutputPacket


# TODO: Consider end of game packet needs (Some kind of flag in output_packet?)


class Rover:
    """
    Main program for controlling the rover.
    """
    LOG_DIR = Path.home() / "Desktop" / "Logs"
    timestamp = datetime.now().strftime("%Y-%m-%d_%H-%M-%S")
    POS_LOG_FILE = LOG_DIR / f"robot_path_{timestamp}.csv"
    NANO_LOG_FILE = LOG_DIR / f"main_log_{timestamp}.log"

    PATH_DIR = Path.home() / "Desktop/RobotPath"
    PATH_FILE = PATH_DIR / f"robot_path.csv"

    def __init__(self):
        # Position from OTOS
        self.position = self.get_initial_transform().get_position()  # Current position
        self.rotation = self.get_initial_transform().rotation  # Current rotation in degrees
        self.light_detected = False
        self.LOG_DIR.mkdir(parents=True, exist_ok=True)

        # Position from encoder feedback
        self.encoder_transform = self.get_initial_transform().get_vector3()

        # Position from theoretical events
        self.theoretical_transform = self.get_initial_transform().get_vector3()

        self.logger = logging.getLogger("Nano")
        self._set_up_logger()

        # Set up packet
        self.input_packet = InputPacket()
        self.output_packet = OutputPacket()

        # Connect packet signals
        def _on_sweeper_flag_changed(flag):
            return
            # if not self.output_packet.game_started: return
            # self.output_packet.set_sweeper_flag(-1 if flag else 1) # 1 is truth-y (acts as True)
        self.input_packet.sweeper_flag_changed.connect(_on_sweeper_flag_changed)

        def _on_auger_flag_changed(flag):
            return
            # if self.output_packet.game_started: return
            # self.output_packet.set_auger_flag(-1 if flag else 1)
        self.input_packet.auger_flag_changed.connect(_on_auger_flag_changed)

        self.input_packet.start_led_switch_changed.connect(self._on_light_detected)
        self.input_packet.gsc_pressure_sensor_changed.connect(self._on_gsc_pressure_sensor_changed)
        self.input_packet.nsc_pressure_sensor_changed.connect(self._on_nsc_pressure_sensor_changed)
        self.input_packet.gsc_limit_switch_changed.connect(self._on_gsc_limit_switch_changed)
        self.input_packet.nsc_limit_switch_changed.connect(self._on_nsc_limit_switch_changed)

        self.input_packet.gsc_limit_switch_changed.connect(self.log_point_to_csv)



        # Initialize Arduino communication
        if sys.platform.startswith('win'):  # Specifically startswith, because Darwin is mac, and has win in it
            self.arduino_comms = ArduinoCommunicator(port="COM4", output_packet=self.output_packet, baud_rate=115200)
        else:
            self.arduino_comms = ArduinoCommunicator(port="/dev/ttyACM0", output_packet=self.output_packet, baud_rate=115200)
        self.arduino_comms.connect()
        self.arduino_comms.packet_received.connect(self.input_packet.receive_packet)

        self.feedback_pos = self.get_initial_transform().get_vector3()

        # Initialize EventHandler
        self.event_handler = EventHandler(self.arduino_comms, input_packet = self.input_packet,
                                          output_packet=self.output_packet)
        self.event_handler.feedback_received.connect(self._on_feedback_received)
        self.event_handler.event_completed.connect(self._on_event_completed)
        self.event_handler.request_transform.connect(self.poll_OTOS)
        self.event_handler.container_loaded.connect(self._on_container_loaded)
        def _on_output_packet_request(): return self.output_packet
        self.event_handler.request_output_packet.connect(_on_output_packet_request)

        # Initialize StateMachine
        self.state_machine = StateMachine()
        self.state_machine.request_light_detected.connect(self._on_request_light_detected)
        self.state_machine.path_requested.connect(self._on_path_requested)
        self.state_machine.point_marked.connect(self._on_point_marked)
        self.state_machine.reset_tracking.connect(self._on_reset_Track)
        self.state_machine.current_transform_requested.connect(self.poll_OTOS)

        self.event_handler.move_to_gsc.connect(self.state_machine.pass_move_to_gsc)
        self.event_handler.move_to_nsc.connect(self.state_machine.pass_move_to_nsc)
        self.event_handler.expand_rover.connect(self.state_machine.pass_expand_rover)

        # Initialize OTOS:
        if not sys.platform.startswith('win'):
            self.OTOS = qwiic_otos.QwiicOTOS()
            self._set_up_OTOS()
        else:
            self.OTOS = None

        o_transform = Vector3(self.position.x, self.position.y, self.rotation)
        self.log_position_to_csv(self.theoretical_transform, o_transform, self.encoder_transform)
        self.logger.debug(f"Starting Position - x:{self.encoder_transform.x}, y:{self.encoder_transform.y}, "
                          f"rot:{self.encoder_transform.rot}")
        self.event_handler.current_event_number += 1

        self.testing = False

    def _set_up_logger(self):
        self.logger = logging.getLogger("Nano")
        self.logger.setLevel(logging.DEBUG)

        print_handler = logging.StreamHandler(stream=sys.stdout)
        frmt = logging.Formatter(
            "%(name)s: %(asctime)s | %(levelname)s | %(filename)s:%(lineno)s | %(process)d >>> %(message)s")
        print_handler.setFormatter(frmt)
        print_handler.setLevel(logging.INFO)

        file_handler = logging.FileHandler(self.NANO_LOG_FILE)
        file_handler.setFormatter(frmt)
        file_handler.setLevel(logging.DEBUG)

        self.logger.addHandler(file_handler)
        self.logger.addHandler(print_handler)

        self.logger.info("Nano Logger finished setup.")

    def _set_up_OTOS(self) -> None:
        # if not self.OTOS:  # For debugging,
        #     return
        # Check if it's connected
        if not self.OTOS.is_connected():
            print("The device isn't connected to the system. Please check your connection",
                  file=sys.stderr)
            self.logger.error("OTOS isn't connected to system.")
            return

        # Initialize the device
        self.OTOS.begin()

        # Calibrate the IMU, which removes the accelerometer and gyroscope offsets
        self.OTOS.calibrateImu()

        # Reset the tracking algorithm - this resets the position to the origin,
        # but can also be used to recover from some rare tracking errors
        self.OTOS.resetTracking()

    def _on_reset_Track(self) -> None:
        self.OTOS.resetTracking()
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

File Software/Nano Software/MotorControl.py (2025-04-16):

import logging

from State import *
from Signal import *

ANGLE_K = .005
TOL_A = 4

class OutputPacket(SignalEmitter):
    left_wheel_speed:float
    right_wheel_speed:float
    auger_flag: int
    sweeper_flag: int
    beacon_arm_flag: int
    beacon_gripper_flag: int
    gsc_gripper_flag: int
    nsc_gripper_flag: int
    gsc_leaner_flag: int
    nsc_leaner_flag: int

    def __init__(self):
        super().__init__()
        self.left_wheel_speed = 0
        self.right_wheel_speed = 0
        self.auger_flag = 0
        self.sweeper_flag = 0
        self.beacon_arm_flag = 0
        self.beacon_gripper_flag = 0
        self.gsc_gripper_flag = 0
        self.nsc_gripper_flag = 0
        self.gsc_leaner_flag = 0
        self.nsc_leaner_flag = 0

        self.game_started = False
        self.game_ended = True

    def __str__(self):
        return (f"{self.left_wheel_speed},{self.right_wheel_speed},{self.auger_flag},{self.sweeper_flag},"
                +f"{self.beacon_arm_flag},{self.beacon_gripper_flag},0,{self.nsc_gripper_flag},"
                 +f"0,{self.nsc_leaner_flag}"+"\n")

    async def set_motor_speed_translation(self, current_position: Transform, target_position: Transform, direction,
                                          testing = True) -> None:
        angle = current_position.get_rotation_to_target(target_position.get_position())
        move_amount = current_position.position.distance_to(target_position.position)
        speed = 50
        speed = speed * direction
        ramp = move_amount * 0.05

        if testing:
            self.left_wheel_speed = 100
            self.right_wheel_speed = 100

        if angle > 180:
            angle = angle - 360 # this might should be 359, but this will give a negative angle to indicate left drift

        angle_k2 = angle * ANGLE_K # this will give a decreasing factor
        angle_k1 = (angle * ANGLE_K) + 1 # this will give an increasing factor

        # DM - I think this should be (1 + ANGLE_K) * angle and (1-ANGLE_K) * angle


        # this looks like it corrects while translating
        if TOL_A >= angle > -TOL_A:
            self.left_wheel_speed = speed
            self.right_wheel_speed = speed
        elif angle > TOL_A:
            self.left_wheel_speed = speed * angle_k2
            self.right_wheel_speed = speed * angle_k1
        elif angle < -TOL_A:
            self.right_wheel_speed = speed * angle_k2
            self.left_wheel_speed = speed * angle_k1

    # this function is simple and may require some tweaking but should work more or less

    # TODO implement some kind of ramping\

    # separate move case for other types of movements
    async def set_motor_speed(self, current_position: Transform, target_position: Transform, rot_right_amount: int,
                              rot_left_amount: int, stop: bool = False, back_slow: bool = False ) -> None:

        angle = current_position.get_rotation_to_target(target_position.get_position())

        #rotated: int = 0 # AC - Did this to stop errors # DM - removed rotated altogether
        if stop:
            self.left_wheel_speed = 0
            self.right_wheel_speed = 0
        if back_slow:
            self.left_wheel_speed = -10 # backup slowly at 10% speed
            self.right_wheel_speed = -10
        if rot_right_amount != 0:
            #DM - fixed - need to get amount needed to rotate in degrees, if we can it would be nice to track the amount weve rotated based off the otis
            #rotated = rotated + 0# amount rotated, cumulative from otos
            if angle <= 2:      # angle is the difference between otos and target angle. 2 provides some room for error
                self.left_wheel_speed = 30
                self.right_wheel_speed = -30
            else :
                self.left_wheel_speed = 0
                self.right_wheel_speed = 0
        if rot_left_amount != 0:
            #DM - fixed - need to get amount needed to rotate in degrees, if we can it would be nice to track the amount weve rotated based off the otis
            #rotated = rotated + 0# amount rotated, cumulative from otis
            if angle <= 2:
                self.left_wheel_speed = -30
                self.right_wheel_speed = 30
            else :
                self.left_wheel_speed = 0
                self.right_wheel_speed = 0




    async def move_forward(self):
        self.left_wheel_speed = 40
        self.right_wheel_speed = 40

    async def move_back(self):
        self.left_wheel_speed = -40
        self.right_wheel_speed = -40

    async def move_back_slower(self):
        self.left_wheel_speed = -35
        self.right_wheel_speed = -35

    async def rotate_right(self):
        self.left_wheel_speed = 40
        self.right_wheel_speed = -40

    async def rotate_left(self):
        self.left_wheel_speed = -40
        self.right_wheel_speed = 40

    async def dont_move(self):
        self.left_wheel_speed = 0
        self.right_wheel_speed = 0

    def set_auger_flag(self, auger_flag: int):
        self.auger_flag = auger_flag

        # auger flag should be set at the start based off start led

    def set_sweeper_flag(self, sweeper_flag: int):
        logger = logging.getLogger("Nano")
        logger.debug(f"Sweeper flag switched: {sweeper_flag}")
        self.sweeper_flag = sweeper_flag

        # sweeper flag should be set at the start based off start led


    def set_beacon_arm_flag(self, beacon_arm_flag: int):
        self.beacon_arm_flag = beacon_arm_flag

        '''
        get in position, will have to come from testing navigation
        set beacon arm flag to high
        await.rover_wait(3) 
        set beacon arm to 0
            call beacon gripper function\
        back up robot
        set beacon arm to -1
        await.rover_wait(3) 

        '''

    def set_beacon_gripper_flag(self, beacon_gripper_flag: int):
        self.beacon_gripper_flag = beacon_gripper_flag

        '''
        set beacon gripper flag to 1
        wait while robot open its hand
        set beacon gripper to 0, no need to touch again
        '''

    def set_gsc_gripper_flag(self, _gsc_gripper_flag: int):
        self.gsc_gripper_flag = 0

        '''
        get in position and slowly back into container
        wait for limit switch flag from arduino
        once limit switch flag, stop robot 
        set gripper flag
        '''
    def close_gsc_gripper(self):
        self.set_gsc_gripper_flag(0)

    def open_gsc_gripper(self):
        self.set_nsc_gripper_flag(0)

    def set_nsc_gripper_flag(self, nsc_gripper_flag: int):
        self.nsc_gripper_flag = nsc_gripper_flag
        '''
        wait until pressure sensor is pressed
        then set flag to 0
        '''
    def close_nsc_gripper(self):
        self.set_nsc_gripper_flag(-1)

    def open_nsc_gripper(self):
        self.set_nsc_gripper_flag(1)

    def set_gsc_leaner_flag(self, gsc_leaner_flag: int):
        self.gsc_leaner_flag = gsc_leaner_flag
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

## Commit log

2024-09-25 Update Project Proposal Draft2.md
    Removed section in "Sensors for location and navigation" under "Problem"
2024-09-25 Update Project Proposal Draft2.md
    Removed extra constraints and measure of success that was attached to one.
2024-09-28 Update Project Proposal Draft2.md
    Update Sensors for localization and navigation to include LiDAR. Updated works cited format.
2024-10-14 Rename Reports/Photos/Sensor_Subsystem_V1.png to Reports/Photos/Conceptual Design/Sensor_Subsystem_V1.png
2024-10-15 Update Conceptual-Design.md
    Added Atomic Subsystem Specifications for Camera
2024-10-15 Update Conceptual-Design.md
    Added a section that was missing from camera subsystem
2024-10-15 Update Conceptual-Design.md
    Add to general sensors potential solutions
2024-10-16 Update Conceptual-Design.md
    Finished version 1 of general sensors section
2024-10-20 Update Conceptual-Design.md
    Ethics layout change. Fixed citation 24. Added flowchart and block diagram
2024-10-23 Update Conceptual-Design.md
    Added General Sensor specifications and Sam Hunter contributions
2024-10-26 Update Conceptual-Design.md
    Added high level solution for general sensors. Listed specs for camera. Added general sensors budget to total budget. Added source for line sensor. Added final chosen sensor for each sensor type need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
2024-10-27 Update Conceptual-Design.md
    Added more to camera comparative solutions, as well as camera high level function
2024-10-27 Update Conceptual-Design.md
    Change Power Specifications formatting to listed SHALL statements, adding voltage and current requirements. Also shortened Motor Control High Level Solution summary to concisely include required component data. Made edits to remove motor microcontroller and divert connections to Jetson Nano.
2024-10-28 Added flowchart for high level charts
2024-10-28 Update Conceptual-Design.md
    Updates info to general sensors about IMU. Updated Gantt Chart, Budget, Block Diagram. Add Robot Autonomous Operation Flowchart
2024-11-25 Uploaded Sensors Subsystem Operational Flowchart
2024-11-25 Rename Reports/Photos/Sensors_Subsystem_Operational_Flowchart.svg to Documentation/Images/Sensors Subsystem/Sensors_Subsystem_Operational_Flowchart.svg
    Moved image
2024-11-25 Uploaded Sensors Subsystem Schematic
2024-11-25 Changed Operational Flowchart to light theme
    Light theme matches the schematic theme
2024-11-25 Create Sensors Subsystem Detail Design.md
2024-11-25 Update Sensors Subsystem Detail Design.md
    Fixed spacing error with specific lines.
2024-11-30 Update Sensors Subsystem Detail Design.md
    Added green LED reasoning and fixed typo.
2024-12-01 Update Sensors Subsystem Detail Design.md
    Added Rizvi's suggestions
2024-12-02 Updated Operational Flow Chart
2024-12-08 Rename Documentation/Signoffs/Sensors Subsystem Detail Design.md to Reports/Sensors Subsystem Detail Design.md
    Moved the document to the Reports folder
2024-12-08 Rename Reports/Photos/Auger_Roller.png to Reports/Photos/Motor Detail Design/Auger_Roller.png
2024-12-08 Rename Reports/Photos/Drivetrain.png to Reports/Photos/Motor Detail Design/Drivetrain.png
2024-12-08 Rename Reports/Photos/Drivetrain2.png to Reports/Photos/Motor Detail Design/Drivetrain2.png
2024-12-08 Rename Reports/Photos/LinearActuators.png to Reports/Photos/Motor Detail Design/LinearActuators.png
2024-12-08 Rename Reports/Photos/Model_Auger.png to Reports/Photos/Motor Detail Design/Model_Auger.png
2024-12-08 Rename Reports/Photos/Model_Drivetrain.png to Reports/Photos/Motor Detail Design/Model_Drivetrain.png
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2024-12-08 Rename Reports/Photos/Operational_Flowchart_2-Page-1.drawio (1).png to Reports/Photos/Motor Detail Design/Operational_Flowchart_2-Page-1.drawio (1).png
2024-12-08 Rename Reports/Photos/Operational_Flowchart_2-Page-1.drawio (2).png to Reports/Photos/Motor Detail Design/Operational_Flowchart_2-Page-1.drawio (2).png
2024-12-08 Rename Reports/Photos/Operational_Flowchart_2-Page-1.drawio (3).png to Reports/Photos/Motor Detail Design/Operational_Flowchart_2-Page-1.drawio (3).png
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2024-12-08 Rename Reports/Photos/Operational_Flowchart_2-Page-2.drawio (1).png to Reports/Photos/Motor Detail Design/Operational_Flowchart_2-Page-2.drawio (1).png
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2024-12-08 Rename Sensors Subsystem Schematic.svg to Sensors Subsystem Schematic.svg
2024-12-08 Update and rename SECON Robot Sensors Subsystem.kicad_sch to Sensors Subsystem.kicad_sch
    [Sensors Subsystem.kicad_sch]
2025-01-22 Rename Sensors Subsystem Detail Design.md to Detail Design Sensors Subsystem.md
2025-03-25 Added support for real-time position tracking (not implemented currently) Updated RoverStates.py to use updated coordinate system.
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2025-04-12 Rename Sensors Subsystem Schematic.svg to Sensors Subsystem Schematic.svg
    Moved to all report photos
2025-04-12 Rename Reports/Photos/Buildable Diagram.svg to Reports/Photos/Camera Detail Design/Buildable Diagram.svg
    Moved to own folder
2025-04-12 Rename Reports/Photos/FlowchartObjectandLineDetection.drawio to Reports/Photos/Camera Detail Design/FlowchartObjectandLineDetection.drawio
    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
2025-04-12 Organization and directory name changes. Uploaded first poster version.
    [Sensors Subsystem.kicad_sch]
2025-04-16 Sensor Design Update poster_v2.tex
    Added some info to the sensor design bullet point.
2025-04-16 Updated Jetson Nano code
    Updated Jetson Nano to final version.
2025-04-16 Uploaded BOM
    BOM Organized by category with totals
    [Capstone Total BOM.xlsx]
2025-04-17 BOM Update poster_v2.tex
    Added sensor design update, xcolor package, BOM table, and removed table example comments
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2025-04-24 Rename Reports/Images and Sources/attached_Hall_Effects_drawn.jpg to Reports/Images and Sources/Experimental Analysis/attached_Hall_Effects_drawn.jpg
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
